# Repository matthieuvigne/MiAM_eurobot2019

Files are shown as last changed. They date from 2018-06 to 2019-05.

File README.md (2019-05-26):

# MiAM_eurobot2019
## Electronics and code of MiAM's robot for Eurobot 2019.

This repo contains code and electronics design files related the 2019 Eurobot competition of MiAM,
a French team of former students from MINES ParisTech and Arts et Métiers schools.

For older files related to the 2018 robot setup, see [MiAM_eurobot2018](https://github.com/matthieuvigne/MiAM_eurobot2018) repo.
The 2019 repo started from the 2018, but has adapted to the new robot architecture (motors, sensors...)

See [MiAM website](https://www.miam-robotique.fr/) (in French).

### Contents
 - [**ArduinoFunnyAction**](./ArduinoFunnyAction) and [**ArduinoSlave**](./ArduinoSlave): arduino code for the funny action (experiment) and for the Raspberry pi slave
 of the main robot.
 - [**ConfigRPi**](./ConfigRPi): Inscruction for configuring a raspberry pi to have headless wifi connection and to run our code.
 - [**Electronics**](./Electronics): wiring diagram and PCBs for the main robot.
 - [**RobotCode**](./RobotCode): onboard C++ code, running on Beaglebone Black or Raspberry pi processor.
 - [**miam_py**](./miam_py): a python package for reading and plotting a log file from the robot.
 - [**StrategyViewer**](./StrategyViewer): A GTK+-based viewer for the trajectories for the robots.

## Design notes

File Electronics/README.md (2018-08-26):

# Electronics

This folder contains the general wiring diagram of the robot, along with schematics and PCB files for custom boards,
realised with Kicad.

 - RPiShield: a somewhat generic shield ("hat") for the Raspberry Pi, to make GPIO and serial connections easier. This
 shield exposes, in a well-ordered manner:
	- the I2C port, with several pins to easily wire multiple salves.
	- three SPI ports (SPI0.0, SPI0.1 and SPI1.2), with a buffer protecting the CS line (useful for the L6470 breakout board,
	where this line is driven high at startup, possibly before the Raspberry Pi is powered up).
	- the UART port.
	- both hardware PWM pins.
	- three onboard LEDs.
	- the remaining 8 GPIOs.
 Note that this shield does not include any buffering on GPIOs.

 - library: a folder containing a Kicad library "MiAM", containing random custom parts used in these boards.

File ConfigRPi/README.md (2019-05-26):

# Configuration steps for Raspberry Pi setup.

This guide describes the setup guide for getting a Raspberry Pi 3 working for our robot. Beside OS install, this includes
network configuration and enabling serial ports. Example files are included in this folder for quicker setup.

## OS and ethernet config.

 - Download the latest image of [Raspbian](https://www.raspberrypi.org/downloads/raspbian/)
 (here without desktop, but you can take the desktop image if needed). Current version: 4.14 kernel, release date 2018-06-27.
 - Extract img file to SD card (this creates a partition called rootfs).
 - Enable ssh on startup by creating an empty ssh file in boot partition (not /boot folder).
 - Edit /etc/dhcpcd.conf to have a static fallback address. I will use 192.168.8.2 as the Beaglebone Black uses 192.168.7.2.
 This is done by adding the following lines to the file:
```
define static profile
    profile static_eth0
    static ip_address=192.168.8.2/24

interface eth0
    fallback static_eth0
```

 - Boot the RPi and connect to PC with ethernet.
 - Give a static IP address to your PC: sudo ip addr add 192.168.8.3/24 dev <pc_ethernet_adapter_name>
 - Connect to ssh to RPI (username pi, password raspberry) at 192.168.8.2.
 - Use raspi-config to enable UART, I2C and SPI ports. The corresponding files should appear in /dev/

## Additional package install
 - Connect RPi to the internet, through wifi: use raspi-config for that.
  sudo apt-get update
  sudo apt-get upgrade
 - Update RPi, and install hostapd, dnsmasq (wifi config) rng-tools (for random number / wifi authentification) and i2c utils.
  sudo apt-get install hostapd dnsmasq i2c-tools rng-tools
 - Install glib library.
sudo apt-get install libglib2.0-dev

## Wifi config

We will now configure the wifi adapter to broadcast a network to connect to the raspberry pi.
See: https://www.raspberrypi.org/documentation/configuration/wireless/access-point.md

 - Reset wpa_supplicant config file, if needed (to prevent autoconnect to another wifi network).
 - Use hostapd to create the network: create a file /etc/hostapd/hostapd.conf with the following content:

interface=wlan0
driver=nl80211
bridge=br0
ssid=<NetworkName>
channel=1
wmm_enabled=0
wpa=1
wpa_passphrase=<Password>
wpa_key_mgmt=WPA-PSK
wpa_pairwise=TKIP
rsn_pairwise=CCMP
auth_algs=1

 - Give a static IP address to the raspberry pi: append to /etc/dhcpcd.conf
	interface wlan0
		static ip_address=192.168.6.2/24
		nohook wpa_supplicant

 - Use dnsmasq to run a dhcp server, giving adress to a PC trying to connect to the raspberry.
 Create a file /etc/dnsmasq.conf with the following content:

  interface=wlan0
	dhcp-range=192.168.6.3,192.168.6.20,255.255.255.0,24h

 - Run on startup: edit /etc/default/hostapd to add
	DAEMON_CONF="/etc/hostapd/hostapd.conf"

	sudo systemctl start hostapd
	sudo systemctl start dnsmasq

 - To connect back to another wifi, simply comment the config in /etc/dhcpcd.conf.

## Image creation and usage.

An image with this config was created (with default password, network RaspberryPi/password RaspberryPi) using the following command:
sudo dd bs=4M if=/dev/mmcblk0 | gzip > 20180813-Raspbian4-14.img.gz
To restore, use:
cat 20180813-Raspbian4-14.img.gz | gunzip | dd of=/dev/mmcblk0

20190504-Raspbian4-19.img.gz : newer image, kernel updated to 4.19, GLIBC to 2.28.

## Running match code at startup

For Eurobot, we want our code to start automatically once the boot process is complete. To do that, we use systemd to
launch a script that starts our code. More precisely, it will launch the file /home/pi/MatchCode on startup. If this file
is not present, the boot process continues normally. Note that, once the code has started, it will conflit with
a user-launched code from ssh: to kill it, use ```pkill MatchCode```

 - Create a bash script StartMatchCode.sh to run our code, with the following content:
 ```
 #!/bin/bash
sleep 1
/home/pi/MatchCode
 ```

 - Make this file executable and store it in /etc/init.d directory:

```
 chmod +x StartMatchCode.sh
 sudo cp StartMatchCode.sh /etc/init.d/
```

 - Create the service configuration file, named StartMatchCode.service:

 ```
[Unit]
Description=Start match code
After=multi-user.target
[Service]
Type=simple
ExecStart=/etc/init.d/StartMatchCode.sh
User=pi
[Install]
WantedBy=multi-user.target
```

 - Copy the file to systemd lookup directory, then enable the service:

 ```
sudo cp StartMatchCode.service /lib/systemd/system/
sudo systemctl daemon-reload
sudo systemctl enable StartMatchCode.service
```

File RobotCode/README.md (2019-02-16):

# Robot Code
This folder contains all the code of the on-board main processor of the robot: Beaglebone Black (2018 robot) or Raspberry Pi.
This code, written entirely in C, is organished around a library, named MiAMEurobot, that implements all low-level
functionalities needed to use the robot (mainly port activation, motor and sensor drivers...). This library is
generic, and could be reused for other projects.

This folder also contains:
 - TestSensors: a simple sensor test. This code tests all the sensors of the robot, both for code debugging and wiring testing purposes.
 - EurobotCode: the main code of the robot, used for Eurobot itself.
 - DrivetrainTest: code for a simplified drivetrain used to test new components: motors, encoders...
 - HardwareTests: a set of independant tests for the robot hardware (mainly used for wiring tests).

## Compiling this code

This code is packaged in such a way as to be cross-compiled from a PC. Cross-compiling indeed has several advantages, the main
one being that there is no need to copy the source to the Beaglebone, thus preventing any temptation to developed on the board itself
(which can be a bad idea if for instance the Beaglebone dies - due to a USB cable short-circuit, I once lost code that way), and making
it very easy to replace the Beaglebone by any other. Other advantages include faster compilation, and the possibility to test compilation
without any access to the Beaglebone.

This code relies on the [glib](https://developer.gnome.org/glib/) - this choice was made to have a single, unified external library for the whole code.
Thus, to cross-compile this code, one needs:

 - a C cross compiler targeting arm platforms.
 - the glib-2.0 library, cross-compiled.

To obtain this, you may do you own setup, or follow the provided guide in ARMCrossCompilationSetup.pdf.

*Note: this identical setup can be used for cross-compiling C code to a Raspberry Pi, as it is also an arm processor.*

## Compiling and installing the BBBEurobot library.

This library, like the rest of this code, is packaged using cmake. To install it to the folder `<installPath>`, simply run:

```
	cmake /path/to/BBBEurobot -DCMAKE_INSTALL_PREFIX=<installPath>
	make
	make install
```

Once installed, this library can be imported using pkg-config. During install, the pkg-config file `BBBEurobot.pc` is installed in
`<installPath>/lib/pkgconfig` : this path must thus be added to the `PKG_CONFIG_PATH` variable. To do so, open your `.bashrc` file

```
gedit ~/.bashrc
```

and append the following line :

```
export PKG_CONFIG_PATH=<installPath>/lib/pkgconfig
```

Remember to `source ~/.bashrc` before use.

There is a doxygen documentation for this library in `BBBEurobot/doc`. Simply run `make_documentation.sh` to generate it.

## Running code of the Beaglebone.

Obviously, the code we have written aims at using the BeagleBone GPIOs and serial ports. To access these ports, the Beaglebone needs a
device tree overlay (DTO) file to enable these ports.
A DTO file for BBB-Eurobot, enabeling all the ports exposed on the PCB (plus UART4, which is needed to talk to the servo driver - it wasn't planned
on the PCB but a wire can easily be solder to make this connection. Note that you need a 3.3V to 5V converter).

This file is called Eurobot-00A0.dts, and can be found in the library folder (BBB-Eurobot). To use it, copy this file to the Beaglebone,
then compile it and copy it to /lib/firmware:

```
	dtc -O dtb -o Eurobot-00A0.dtbo -b 00 -@ Eurobot-00A0.dts
	cp Eurobot-00A0.dtbo /lib/firmware
```

Now doing ```echo Eurobot > /sys/devices/bone_capemgr.9/slots``` enables all these ports for the duration of the current boot (this is done internally by BBB-Eurobot).

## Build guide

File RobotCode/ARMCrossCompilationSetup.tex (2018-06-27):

\documentclass[a4paper,11pt]{article}
\usepackage[T1]{fontenc}
\usepackage[utf8]{inputenc}
\usepackage{lmodern}
\usepackage[english]{babel}
\usepackage{hyperref}
\usepackage{listings}

%listings settings
\lstset{
  basicstyle=\ttfamily,
  columns=fullflexible,
  frame=leftline,
  rulecolor=\color{red},
  framerule=2pt,
  xleftmargin=15pt,
  breaklines=true
}

\hypersetup{
  colorlinks   = true, %Colours links instead of ugly boxes
  urlcolor     = blue, %Colour for external hyperlinks
  linkcolor    = black, %Colour of internal links
  citecolor   = black %Colour of citations
}

\title{Cross-compilation environment setup.}
\author{Matthieu Vigne}

\begin{document}
\maketitle
\tableofcontents
\section{Introduction}

\par This guide explains how to setup a cross-compilation environment on a Linux PC (Fedora or Debian/Ubunu) to compile our code, i.e. the BBBEurobot library. This setup works for compiling code to a Beaglebone Black, and to a Raspberry Pi as well.
Three things are needed to cross-compile this code:

 - a C compiler targeting the \emph{armhf} platform, called \textbf{gcc-arm-linux-gnueabihf}.
 
 - a cross-compiled version of the glib, used by our code.
 
 - a renamed \emph{pkg-config} file to load the cross-compiled glib when compiling.
 
\section{Debian setup}

These instructions were tested on Debian 8 (Jessie) in 2015. The setup for Ubuntu is probably quite similar.

Setup on Debian is quite fast, as the official repo already have the compiler and a cross-compiled glib. The only step needed is to tell \emph{apt} to add the arm platform, then install the packages as usual:

\begin{lstlisting}[]
sudo dpkg --add-architecture armhf
sudo apt-get update
sudo apt-get install gcc-arm-linux-gnueabihf
sudo apt-get install libglib2.0-dev:armhf
\end{lstlisting}

Now everything is installed, but there is one last setup step needed: link to the \emph{pkg-config} file of the glib. Since it has the same name as the one installed for your system library version, we will rename it to prevent any conflict. To keep things clear, I advise you modify (freely) the \emph{Name:} and \emph{Description:} fields of this file, \emph{/usr/lib/arm-linux-gnueabihf/pkgconfig/glib-2.0.pc} though for instance the following command:

\begin{lstlisting}
sudo nano /usr/lib/arm-linux-gnueabihf/pkgconfig/glib-2.0.pc
\end{lstlisting}

Then, simply copy this file to the default \emph{pkg-config} search path, renaming it:

\begin{lstlisting}[]
sudo mv /usr/lib/arm-linux-gnueabihf/pkgconfig/glib-2.0.pc /usr/share/pkgconfig/armglib-2.0.pc
\end{lstlisting}

To check that everything works correctly, type:

\begin{lstlisting}[]
pkg-config --list-all | grep arm
\end{lstlisting}

This should give you the \emph{armglib-2.0} library, with the name and description you previously entered.

\section{Fedora setup}

These instructions were tested in Febuary 2018 on Fedora 27.

Contrary to Debian, the official Fedora repo do not contain either the compiler nor the cross-compiled glib. We will get the compiler from an unofficial Copr repo, and then cross-compile the glib from source.

First, install the compiler and cross-compiled glibc (for basic C functions: this is a dependency of glib) using:

\begin{lstlisting}
sudo dnf copr enable lantw44/arm-linux-gnueabihf-toolchain
sudo dnf install arm-linux-gnueabihf-gcc arm-linux-gnueabihf-glibc
\end{lstlisting}

In order to compile the glib, we must first install its dependencies.

The firs is libffi: get the latest version from  \href{https://sourceware.org/libffi/}{https://sourceware.org/libffi/} (v 3.2.1 in Febuary 2018), decompress it, then run from the source folder:

\begin{lstlisting}[]
./configure --host=arm-linux-gnueabihf --prefix=/usr/arm-linux-gnueabihf/sys-root/
make
sudo make install
\end{lstlisting}

The first line configures the build, telling the system to cross-compile the library using the cross-compiler instead of system gcc, and to install it in \emph{/usr/arm-linux-gnueabihf/sys-root/}, the path used on install of the compiler and glibc. Then we compile and install the library.

\emph{Note: for faster compilation, you can append \emph{-jN} to the make instruction, where N is the number of process being run in parallel.}

The second dependancy is the zlib (\href{http://www.zlib.net/}{http://www.zlib.net/}, v 1.2.11 in Febuary 2018), installed with the same process:
\begin{lstlisting}[]
CC=arm-linux-gnueabihf-gcc ./configure --prefix=/usr/arm-linux-gnueabihf/sys-root/
make
sudo make install
\end{lstlisting}

Finally, download the glib \href{http://ftp.gnome.org/pub/GNOME/sources/glib/}{http://ftp.gnome.org/\\pub/GNOME/sources/glib/} (v 2.55.1 in Febuary 2018). Go to the parent of the source directory (i.e. where you uncompressed the archive), create a build folder, in which we place a config file \emph{arm.cache}:

\begin{lstlisting}
mkdir build
cd build
gedit arm.cache
\end{lstlisting}

Copy the following content in \emph{arm.cache}:
\begin{lstlisting}[caption= File arm.cache]
glib_cv_long_long_format=ll
glib_cv_stack_grows=no
glib_cv_uscore=yes
ac_cv_func_posix_getpwuid_r=no
ac_cv_func_posix_getgrgid_r=no
LIBFFI_CFLAGS="-I/usr/arm-linux-gnueabihf/sys-root/lib/libffi-3.2.1/include"
LIBFFI_LIBS="-L/usr/arm-gnueabihf/sys-root/lib -lffi"
ZLIB_CFLAGS="-I/usr/arm-linux-gnueabihf/sys-root/include"
ZLIB_LIBS="-L/usr/arm-linux-gnueabihf/sys-root/lib -lz"
\end{lstlisting}

Now, configure the build using the given \emph{arm.cache}:

\begin{lstlisting}[]
../glib-2.55.1/configure --host=arm-linux-gnueabihf --prefix=/usr/arm-linux-gnueabihf/sys-root/ --cache-file=./arm.cache --with-pcre --enable-libmount=no
make
sudo make install
\end{lstlisting}

Comments: the option --with-pcre tells the configuration script to use internally-package pcre library. --enable-libmount=no disables libmount, a library used for disk mounting that we won't be using on the Beaglebone, and hence that wasn't installed (it can otherwise be installed using the same process as before).

Now everything is installed, but there is one last setup step needed: link to the \emph{pkg-config} file of the glib. Since it has the same name as the one installed for your system library version, we will rename it to prevent any conflict. To keep things clear, I advise you modify (freely) the \emph{Name:} and \emph{Description:} fields of this file, \emph{/usr/arm-linux-gnueabihf/sys-root/lib/pkgconfig/glib-2.0.pc} though for instance the following command:

\begin{lstlisting}
sudo nano /usr/arm-linux-gnueabihf/sys-root/lib/pkgconfig/glib-2.0.pc
\end{lstlisting}

Then, simply copy this file to the default \emph{pkg-config} search path, renaming it:

\begin{lstlisting}[]
sudo mv /usr/arm-linux-gnueabihf/sys-root/lib/pkgconfig/glib-2.0.pc /usr/share/pkgconfig/armglib-2.0.pc
\end{lstlisting}

To check that everything works correctly, type:

\begin{lstlisting}[]
pkg-config --list-all | grep arm
\end{lstlisting}

This should give you the \emph{armglib-2.0} library, with the name and description you previously entered.

\end{document}

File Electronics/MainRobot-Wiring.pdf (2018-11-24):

# MiAM main robot electrical architecture

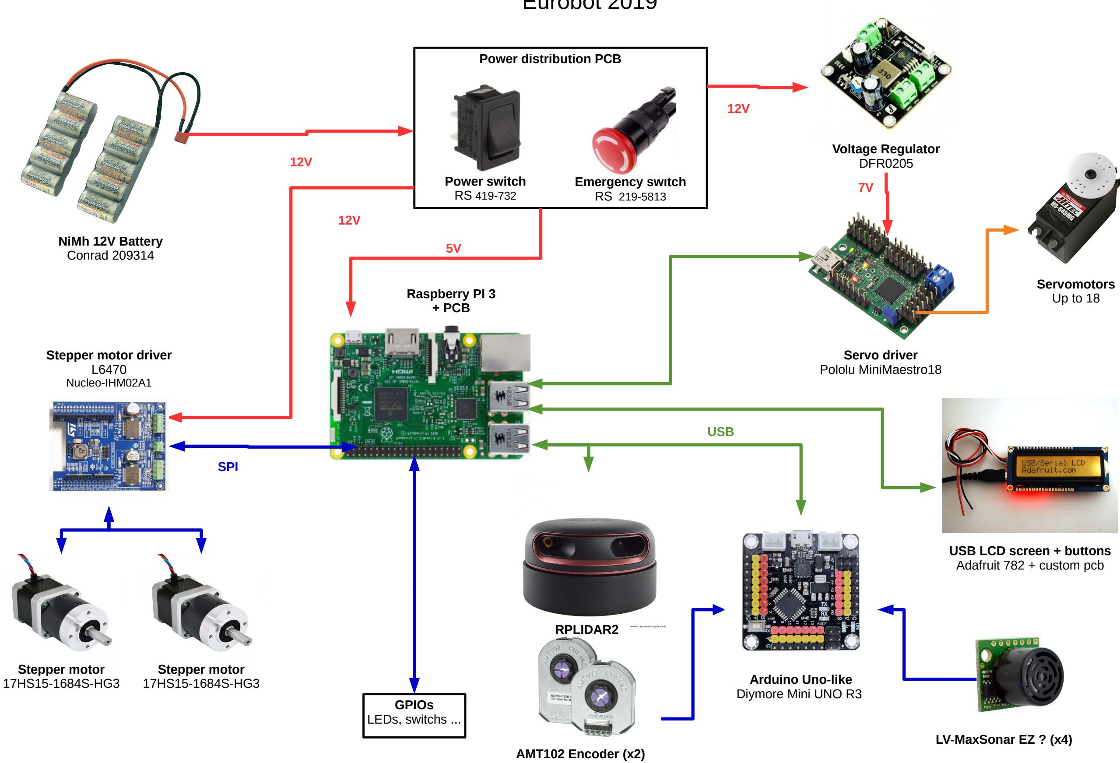
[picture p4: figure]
SPI; NiMh 12V Battery Conrad 209314; Servo driver Pololu MiniMaestro18; Power switch RS 419-732; Emergency switch RS 219-5813; Power distribution PCB; USB; AMT102 Encoder (x2); Arduino Uno-like Diymore Mini UNO R3; LV-MaxSonar EZ ? (x4); Servomotors Up to 18; Voltage Regulator DFR0205; GPIOs LEDs, switchs ...; Raspberry PI 3 + PCB; USB LCD screen + buttons Adafruit 782 + custom pcb; Stepper motor driver L6470 Nucleo-IHM02A1; Stepper motor 17HS15-1684S-HG3; RPLIDAR2

# Eurobot 2019

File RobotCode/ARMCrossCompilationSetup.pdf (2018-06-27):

Cross-compilation environment setup.

Matthieu Vigne

May 27, 2018

## Contents

1 Introduction | 1
2 Debian setup | 1
3 Fedora setup | 2

## 1 Introduction

This guide explains how to setup a cross-compilation environment on a Linux PC (Fedora or Debian/Ubunu) to compile our code, i.e. the BBBEurobot library. This setup works for compiling code to a Beaglebone Black, and to a Raspberry Pi as well. Three things are needed to cross-compile this code:
- a C compiler targeting the armhf platform, called gcc-arm-linux-gnueabihf.
- a cross-compiled version of the glib, used by our code.
- a renamed pkg-config file to load the cross-compiled glib when compiling.

## 2 Debian setup

These instructions were tested on Debian 8 (Jessie) in 2015. The setup for Ubuntu is probably quite similar.
Setup on Debian is quite fast, as the official repo already have the compiler and a cross-compiled glib. The only step needed is to tell apt to add the arm platform, then install the packages as usual:

sudo dpkg --add-architecture armhf
sudo apt-get update
sudo apt-get install gcc-arm-linux-gnueabihf sudo apt-get install libglib2.0-dev:armhf

1

Now everything is installed, but there is one last setup step needed: link to the pkg-config file of the glib. Since it has the same name as the one installed for your system library version, we will rename it to prevent any conflict. To keep things clear, I advise you modify (freely) the Name: and Description: fields of this file, /usr/lib/arm-linux-gnueabihf/pkgconfig/glib-2.0.pc though for instance the following command:

sudo nano /usr/lib/arm-linux-gnueabihf/pkgconfig/glib-2.0.pc

Then, simply copy this file to the default pkg-config search path, renaming it:

sudo mv /usr/lib/arm-linux-gnueabihf/pkgconfig/glib-2.0.pc / usr/share/pkgconfig/armglib-2.0.pc

To check that everything works correctly, type:

pkg-config --list-all | grep arm

This should give you the armglib-2.0 library, with the name and description you previously entered.

## 3 Fedora setup

These instructions were tested in Febuary 2018 on Fedora 27.
Contrary to Debian, the official Fedora repo do not contain either the compiler nor the cross-compiled glib. We will get the compiler from an unofficial Copr repo, and then cross-compile the glib from source.
First, install the compiler and cross-compiled glibc (for basic C functions: this is a dependency of glib) using:

sudo dnf copr enable lantw44/arm-linux-gnueabihf-toolchain sudo dnf install arm-linux-gnueabihf-gcc arm-linux-gnueabihf -glibc

In order to compile the glib, we must first install its dependencies.
The firs is libffi: get the latest version from https://sourceware.org/libffi/(v 3.2.1 in Febuary 2018), decompress it, then run from the source folder:

./configure --host=arm-linux-gnueabihf --prefix=/usr/armlinux-gnueabihf/sys-root/
make
sudo make install

The first line configures the build, telling the system to cross-compile the library using the cross-compiler instead of system gcc, and to install it in /usr/arm-linux-gnueabihf/sys-root/, the path used on install of the compiler and glibc. Then we compile and install the library.
Note: for faster compilation, you can append -jN to the make instruction, where N is the number of process being run in parallel.

2

The second dependancy is the zlib (http://www.zlib.net/, v 1.2.11 in Febuary 2018), installed with the same process:

CC=arm-linux-gnueabihf-gcc ./configure --prefix=/usr/armlinux-gnueabihf/sys-root/
make
sudo make install

Finally, download the glib http://ftp.gnome.org/pub/GNOME/sources/glib/ (http://ftp.gnome.org/pub/GNOME/sources/glib/) (v 2.55.1 in Febuary 2018). Go to the parent of the source directory (i.e. where you uncompressed the archive), create a build folder, in which we place a config file arm.cache:

mkdir build
cd build
gedit arm.cache

Copy the following content in arm.cache:

Listing 1: File arm.cache

glib_cv_long_long_format=ll glib_cv_stack_grows=no
glib_cv_uscore=yes
ac_cv_func_posix_getpwuid_r=no ac_cv_func_posix_getgrgid_r=no LIBFFI_CFLAGS="-I/usr/arm-linux-gnueabihf/sys-root/lib/ libffi-3.2.1/include"
LIBFFI_LIBS="-L/usr/arm-gnueabihf/sys-root/lib -lffi" ZLIB_CFLAGS="-I/usr/arm-linux-gnueabihf/sys-root/include" ZLIB_LIBS="-L/usr/arm-linux-gnueabihf/sys-root/lib -lz"

Now, configure the build using the given arm.cache:

../glib-2.55.1/configure --host=arm-linux-gnueabihf --prefix =/usr/arm-linux-gnueabihf/sys-root/ --cache-file=./arm. cache --with-pcre --enable-libmount=no
make
sudo make install

Comments: the option –with-pcre tells the configuration script to use internally-package pcre library. –enable-libmount=no disables libmount, a library used for disk mounting that we won’t be using on the Beaglebone, and hence that wasn’t installed (it can otherwise be installed using the same process as before).
Now everything is installed, but there is one last setup step needed: link to the pkg-config file of the glib. Since it has the same name as the one installed for your system library version, we will rename it to prevent any conflict. To keep things clear, I advise you modify (freely) the

3

Name: and Description: fields of this file, /usr/arm-linux-gnueabihf/sys-root/lib/pkgconfig/glib-2.0.pc though for instance the following command:

sudo nano /usr/arm-linux-gnueabihf/sys-root/lib/pkgconfig/ glib-2.0.pc

Then, simply copy this file to the default pkg-config search path, renaming it:

sudo mv /usr/arm-linux-gnueabihf/sys-root/lib/pkgconfig/glib -2.0.pc /usr/share/pkgconfig/armglib-2.0.pc

To check that everything works correctly, type:

pkg-config --list-all | grep arm

This should give you the armglib-2.0 library, with the name and description you previously entered.

4

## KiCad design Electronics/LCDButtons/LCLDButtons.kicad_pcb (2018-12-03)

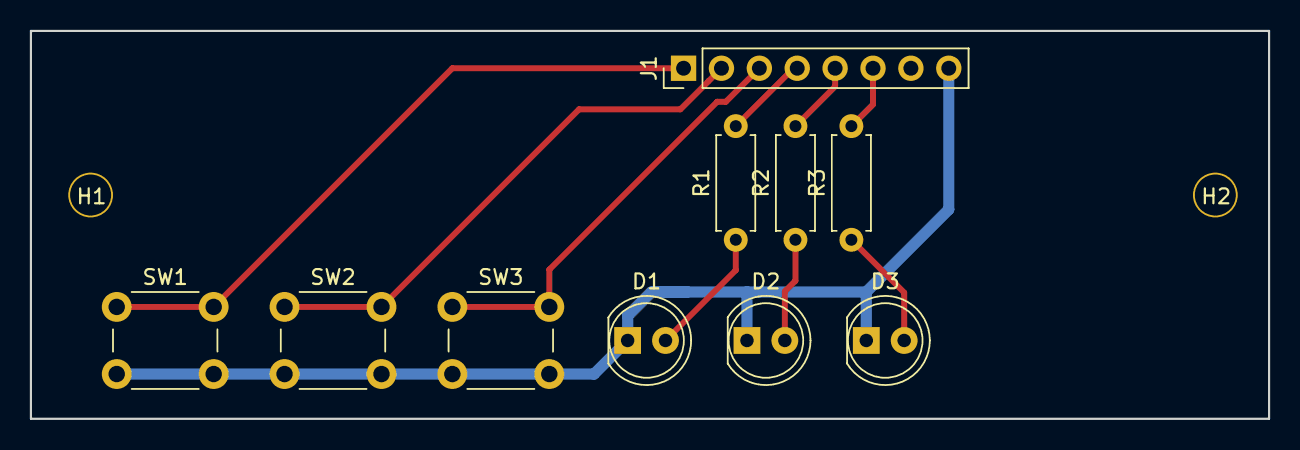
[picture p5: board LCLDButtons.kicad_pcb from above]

Board: 2 copper layers, 83.0 x 26.0 mm, 12 parts (0 on the bottom side), 10 nets.

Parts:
D1, D2, D3: LED; LED_D5.0mm
H1, H2: Hole_3mm_PTH; NPTH_3mm_ID
J1: Conn_01x08; Pin_Header_Straight_1x08_Pitch2.54mm
R1, R2, R3: 1k; R_Axial_DIN0207_L6.3mm_D2.5mm_P7.62mm_Horizontal
SW1, SW2, SW3: SW_SPST; SW_PUSH_6mm

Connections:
/PB0: J1.4, R1.2
/PC2: J1.3, SW3.1
/PC4: J1.2, SW2.1
/PC7: J1.1, SW1.1
/RX: J1.6, R3.2
/TX: J1.5, R2.2
GND: D1.1, D2.1, D3.1, J1.8, SW1.2, SW2.2, SW3.2
unnamed: D1.2, R1.1
unnamed: D2.2, R2.1
unnamed: D3.2, R3.1

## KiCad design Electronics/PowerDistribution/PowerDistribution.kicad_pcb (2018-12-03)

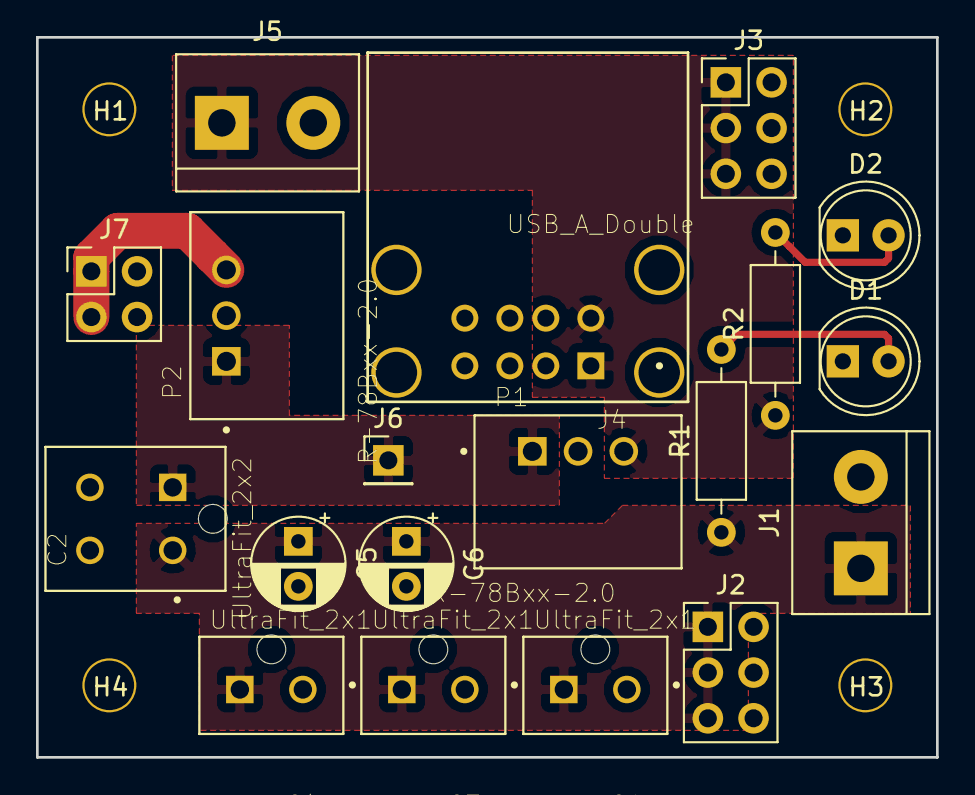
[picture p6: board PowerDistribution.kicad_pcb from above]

Board: 2 copper layers, 50.0 x 40.0 mm, 23 parts (0 on the bottom side), 7 nets.

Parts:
C1, C3, C4: UltraFit_2x1; MOLEX_1722861102
C2: UltraFit_2x2; MOLEX_1722981104
C5, C6: CP1; CP_Radial_D5.0mm_P2.50mm
D1, D2: LED; LED_D5.0mm
H1, H2, H3, H4: Hole_3mm_PTH; NPTH_3mm_ID
J1, J5: Screw_Terminal_01x02; TerminalBlock_bornier-2_P5.08mm
J2, J3: Conn_02x03_Odd_Even; PinHeader_2x03_P2.54mm_Vertical
J4: USB_A_Double; USB_A_Double_2410_05
J6: Conn_01x01_Male; PinHeader_1x01_P2.54mm_Vertical
J7: Conn_02x02_Odd_Even; PinHeader_2x02_P2.54mm_Vertical
P1, P2: R-78Bxx-2.0; CONV_R-78Bxx-2.0
R1: 2k; R_Axial_DIN0207_L6.3mm_D2.5mm_P10.16mm_Horizontal
R2: 600; R_Axial_DIN0207_L6.3mm_D2.5mm_P10.16mm_Horizontal

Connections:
+12V: C2.1, J6.1, P1.1, P2.1
GND: C1.2, C2.4, C3.2, C4.2, C5.2, C6.2, D1.1, D2.1, J1.2, J2.2, J2.4, J2.6, J3.2, J3.4, J3.6, J4.4, J5.2, J7.2, J7.4, P1.2, P2.2
unnamed: C1.1, C2.2, C3.1, C4.1, C5.1, C6.1, J1.1, J2.1, J2.3, J2.5, R1.1
unnamed: D1.2, R1.2
unnamed: D2.2, R2.2
unnamed: J3.1, J3.3, J3.5, J4.1, J5.1, P1.3, R2.1
unnamed: J7.1, J7.3, P2.3

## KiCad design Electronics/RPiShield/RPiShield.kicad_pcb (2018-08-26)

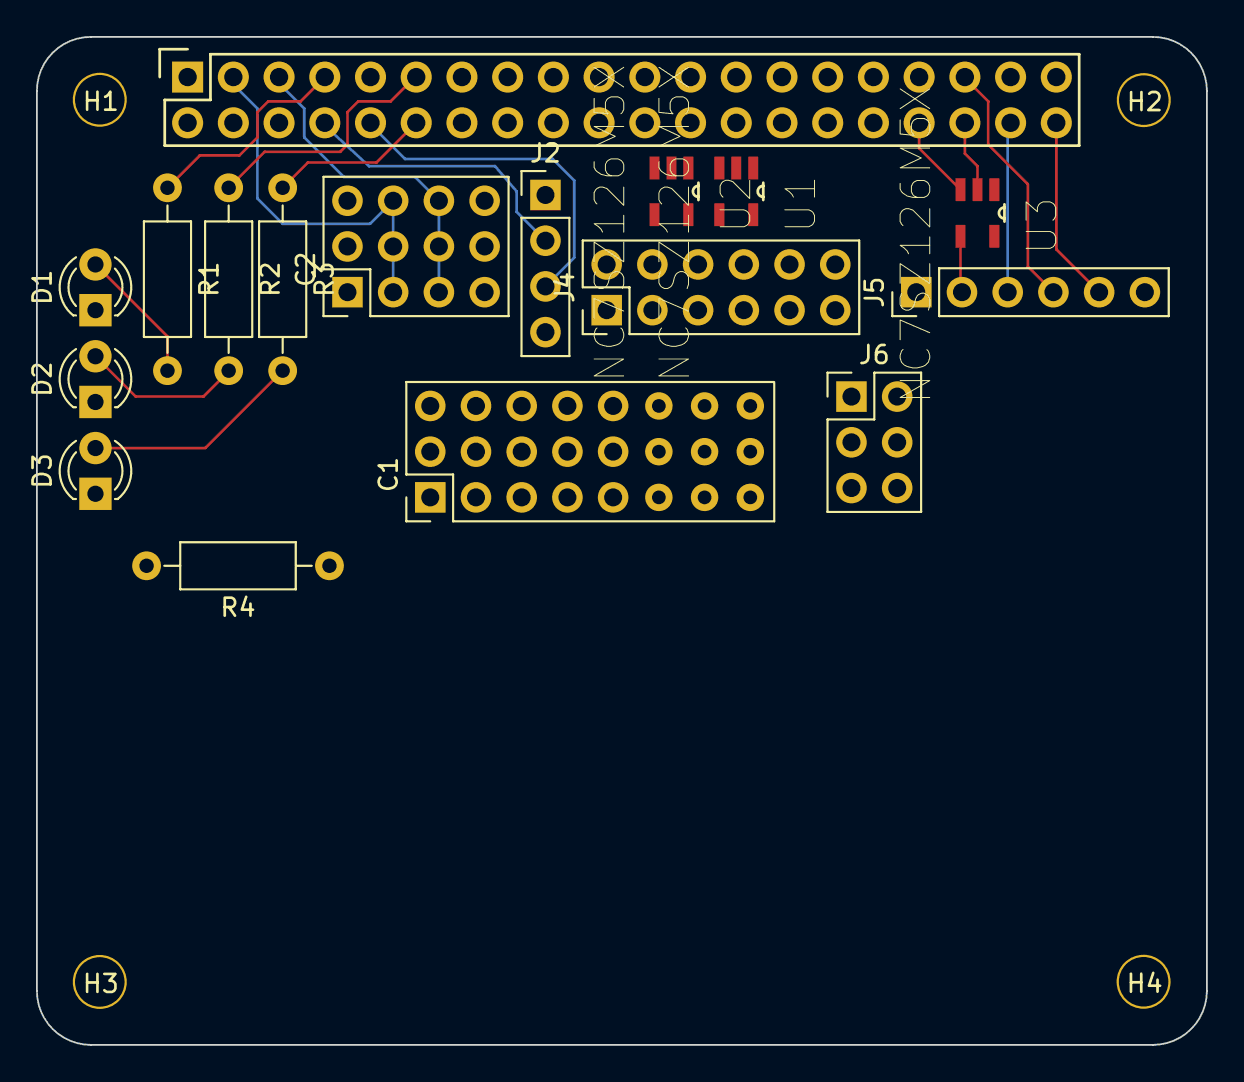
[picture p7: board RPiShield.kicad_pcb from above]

Board: 2 copper layers, 65.0 x 56.0 mm, 21 parts (0 on the bottom side), 35 nets.

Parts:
C1: Conn_03x08; Pin_Header_Straight_3x08_Pitch2.54mm
C2: Conn_03x04; Pin_Header_Straight_3x04_Pitch2.54mm
D1, D2, D3: LED; LED_D3.0mm
H1, H2, H3, H4: Hole_3mm_PTH; NPTH_3mm_ID
J1: PI40HAT; Socket_Strip_Straight_2x20
J2: Conn_01x04; Pin_Header_Straight_1x04_Pitch2.54mm
J4: Conn_02x06_Odd_Even; Pin_Header_Straight_2x06_Pitch2.54mm
J5: Conn_01x06; Pin_Header_Straight_1x06_Pitch2.54mm
J6: Conn_02x03_Odd_Even; Pin_Header_Straight_2x03_Pitch2.54mm
R1, R2, R3: 220; R_Axial_DIN0207_L6.3mm_D2.5mm_P10.16mm_Horizontal
R4: 20k; R_Axial_DIN0207_L6.3mm_D2.5mm_P10.16mm_Horizontal
U1, U2, U3: NC7SZ126M5X

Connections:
+3V3: C1.2, C1.5, C1.8, C1.11, C1.14, C1.17, C1.20, C1.23, C2.1, C2.2, C2.3, J1.1, J1.17, J2.1, J4.1, J4.2, J5.1, J6.3, J6.4, R4.1, U1.1, U1.5, U2.1, U2.5, U3.1, U3.5
+5V: J1.2, J1.4
/GPIO_5: C1.18, J1.29
/GPIO_6: C1.21, J1.31
/GPIO_12_PWM0: J1.32, J6.1
/GPIO_13_PWM1: J1.33, J6.2
/GPIO_22: C1.6, J1.15
/GPIO_23: C1.9, J1.16
/GPIO_24: C1.12, J1.18
/GPIO_25: C1.15, J1.22
/GPIO_26: C1.24, J1.37
/GPIO_27: C1.3, J1.13
/I2C_SCL: C2.7, C2.8, C2.9, J1.5
/I2C_SDA: C2.4, C2.5, C2.6, J1.3
/SPI0_CLK: J1.23, J4.9, J4.10
/SPI0_MISO: J1.21, J4.7, J4.8
/SPI0_MOSI: J1.19, J4.5, J4.6
/SPI0_SS0: J1.24, U1.2
/SPI0_SS1: J1.26, U2.2
/SPI1_CLK: J1.40, J5.5
/SPI1_MISO: J1.35, J5.4
/SPI1_MOSI: J1.38, J5.3
/SPI1_SS2: J1.36, U3.2
/UART_RX: J1.10, J2.3
/UART_TX: J1.8, J2.2
GND: C1.1, C1.4, C1.7, C1.10, C1.13, C1.16, C1.19, C1.22, C2.10, C2.11, C2.12, D1.1, D2.1, D3.1, J1.6, J1.9, J1.14, J1.20, J1.25, J1.30, J1.34, J1.39, J2.4, J4.11, J4.12, J5.6, J6.5, J6.6, R4.2, U1.3, U2.3, U3.3
unnamed: D1.2, R1.2
unnamed: D2.2, R2.2
unnamed: D3.2, R3.2
unnamed: J1.7, R1.1
unnamed: J1.11, R2.1
unnamed: J1.12, R3.1
unnamed: J4.3, U1.4
unnamed: J4.4, U2.4
unnamed: J5.2, U3.4

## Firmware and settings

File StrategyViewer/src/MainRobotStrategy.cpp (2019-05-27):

/// \author Matthieu Vigne
/// \copyright GNU GPLv3
#include "ViewerRobot.h"
#include <MiAMEurobot/trajectory/Utilities.h>
#include <MiAMEurobot/trajectory/ArcCircle.h>

using namespace miam::trajectory;

// Define robot constants for trajectory generation.
namespace robotdimensions
{
    double const wheelSpacing = 106.0; ///< Wheel spacing from robot center, in mm.
    double const maxWheelSpeedTrajectory = 400; ///< Maximum wheel speed, in mm/s.
    double const maxWheelAccelerationTrajectory = 400; ///< Maximum wheel acceleration, in mm/s^2.
}

// Robot dimension.
double const CHASSIS_FRONT = 150.0;
double const CHASSIS_BACK = 150.0;
double const CHASSIS_WIDTH = 150.0;


void mainRobotStrategy(ViewerRobot &robot)
{
    robot.trajectory_.clear();
    robot.clearScore();
    std::cout << "Computing main robot strategy, obstacle at " << robot.obstacleX_ << " " << robot.obstacleY_ << std::endl;

    // Update config.
    miam::trajectory::setTrajectoryGenerationConfig(robotdimensions::maxWheelSpeedTrajectory,
                                                    robotdimensions::maxWheelAccelerationTrajectory,
                                                    robotdimensions::wheelSpacing);

    // Create required variables.
    RobotPosition targetPosition;
    TrajectoryVector traj;
    RobotPosition endPosition;
    std::vector<RobotPosition> positions;
    bool wasMoveSuccessful = true;

    // Set initial position
    targetPosition.x = CHASSIS_WIDTH + 75;
    targetPosition.y = 1100 + CHASSIS_FRONT + 30;
    targetPosition.theta = -M_PI_2;
    robot.resetPosition(targetPosition, true, true, true);

    //**********************************************************
    // Go get first atoms.
    //**********************************************************
    targetPosition.y = CHASSIS_FRONT + 50;
    traj = miam::trajectory::computeTrajectoryStraightLineToPoint(robot.getCurrentPosition(), targetPosition);
    robot.setTrajectoryToFollow(traj);
    wasMoveSuccessful = robot.waitForTrajectoryFinished();

    //~ getAtoms();
    //~ robot.moveRail(0.05);
    //~ robot.servos_.moveSuction(false);

    // Move back on base, drop all three atoms.
    targetPosition.y = 1710;
    traj = miam::trajectory::computeTrajectoryStraightLineToPoint(robot.getCurrentPosition(), targetPosition, 0.0, true);
    robot.setTrajectoryToFollow(traj);
    // Atom drop
    int suctionOrder[3] = {2, 1, 0};
    if (robot.isPlayingRightSide())
    {
        suctionOrder[0] = 0;
        suctionOrder[2] = 2;
    }
    //~ while (!robot.isTrajectoryFinished())
    //~ {
        //~ targetPosition = robot.getCurrentPosition();
        //~ if (targetPosition.y > 950)
        //~ {
            //~ robot.servos_.tapOpen();
            //~ robot.servos_.openTube(suctionOrder[0]);
        //~ }
        //~ if (targetPosition.y > 1300)
            //~ robot.servos_.openTube(suctionOrder[1]);
        //~ if (targetPosition.y > 1600)
            //~ robot.servos_.openTube(suctionOrder[2]);
        //~ usleep(20000);
    //~ }
    if (wasMoveSuccessful)
        robot.updateScore(18); // 3 atoms with the right color inside the zone.
    //~ robot.moveRail(0.3);
    //~ robot.servos_.moveSuction(true);


    //**********************************************************
    // Get second set of atoms.
    //**********************************************************

    // Go get left set of three atoms, following a curved trajectory.
    targetPosition = robot.getCurrentPosition();
    positions.push_back(targetPosition);
    targetPosition.x = 500;
    positions.push_back(targetPosition);
    targetPosition.x += 220;
    targetPosition.y -= 40;
    positions.push_back(targetPosition);
    targetPosition.y = 800;
    positions.push_back(targetPosition);
    targetPosition.x = 600;
    targetPosition.y = 700;
    positions.push_back(targetPosition);
    targetPosition.y = 510 + CHASSIS_FRONT;
    positions.push_back(targetPosition);
    traj = miam::trajectory::computeTrajectoryRoundedCorner(positions, 100.0, 0.05);
    robot.setTrajectoryToFollow(traj);
    wasMoveSuccessful = robot.waitForTrajectoryFinished();

    // Grab atoms.
    bool hasAtoms = false;
    if (wasMoveSuccessful)
    {
        //~ getAtoms();
        hasAtoms = true;
    }
    targetPosition = robot.getCurrentPosition();
    traj = miam::trajectory::computeTrajectoryStraightLine(targetPosition, -150);
    robot.setTrajectoryToFollow(traj);
    robot.waitForTrajectoryFinished();

    //~ robot.moveRail(0.05);
    //~ robot.servos_.moveSuction(false);

    // Go drop atoms.
    // Drop everything in the red zone, pushing the tree atoms on the field.
    positions.clear();
    targetPosition = robot.getCurrentPosition();
    positions.push_back(targetPosition);
    targetPosition.y = 1550;
    positions.push_back(targetPosition);
    targetPosition.x = 450;
    positions.push_back(targetPosition);
    traj = miam::trajectory::computeTrajectoryRoundedCorner(positions, 150.0, 0.05);
    robot.setTrajectoryToFollow(traj);
    wasMoveSuccessful = robot.waitForTrajectoryFinished();

    //~ robot.servos_.tapOpen();
    //~ robot.servos_.openTube(0);
    //~ robot.servos_.openTube(1);
    //~ robot.servos_.openTube(2);
    if (wasMoveSuccessful)
        robot.updateScore(13); // Three atoms pushed in the zone, two of the right color.
    if (hasAtoms)
        robot.updateScore(13); // Three atoms dropped in the zone, two of the right color.

    // Move back
    targetPosition = robot.getCurrentPosition();
    traj = miam::trajectory::computeTrajectoryStraightLine(targetPosition, -150);
    robot.setTrajectoryToFollow(traj);
    robot.waitForTrajectoryFinished();

    //**********************************************************
    // Drop the blue atom in the particle accelerator.
    //**********************************************************
    targetPosition = robot.getCurrentPosition();
    positions.clear();
    positions.push_back(targetPosition);
    targetPosition.x = 1300;
    positions.push_back(targetPosition);
    targetPosition.x = 1600;
    targetPosition.y = 2000 - CHASSIS_WIDTH - 130;
    positions.push_back(targetPosition);
    targetPosition.x = 1620;
    positions.push_back(targetPosition);
    traj = miam::trajectory::computeTrajectoryRoundedCorner(positions, 80.0, 0.1);
    robot.setTrajectoryToFollow(traj);
    //~ usleep(100000);
    //~ while (!robot.isTrajectoryFinished())
    //~ {
        //~ targetPosition = robot.getCurrentPosition();
        //~ if (targetPosition.x > 1250)
        //~ {
            //~ robot.servos_.unfoldArms(robot.isPlayingRightSide());
            //~ break;
        //~ }
    //~ }
    wasMoveSuccessful = robot.waitForTrajectoryFinished();
    //~ robot.servos_.raiseArms(robot.isPlayingRightSide());
    if (wasMoveSuccessful)
    {
        robot.updateScore(20); // 20 pts: atom + goldium release.

        //**********************************************************
        // Get the goldium atom.
        //**********************************************************
        //~ robot.moveRail(1.0);
        //~ robot.servos_.moveSuction(true);
        targetPosition = robot.getCurrentPosition();
        targetPosition.x = 3000 - 770;
        targetPosition.y = 1650;
        traj = miam::trajectory::computeTrajectoryStraightLineToPoint(robot.getCurrentPosition(), targetPosition);
        endPosition = targetPosition;
        endPosition.y = 2000 - CHASSIS_FRONT - 100;
        traj = traj + miam::trajectory::computeTrajectoryStraightLineToPoint(targetPosition, endPosition);
        robot.setTrajectoryToFollow(traj);
        wasMoveSuccessful = robot.waitForTrajectoryFinished();

        if (wasMoveSuccessful)
        {
            //~ robot.servos_.tapClose();
            //~ robot.servos_.closeTube(0);
            //~ robot.servos_.openTube(1);
            //~ robot.servos_.closeTube(2);
            //~ robot.servos_.turnOnPump();
            //~ usleep(500000);
            targetPosition = robot.getCurrentPosition();
            traj = miam::trajectory::computeTrajectoryStraightLine(targetPosition, 40);
            robot.setTrajectoryToFollow(traj);
            robot.waitForTrajectoryFinished();
            //~ usleep(500000);
            //~ robot.servos_.closeTube(2);
            //~ robot.servos_.tapClose();
            //~ usleep(500000);
            //~ robot.servos_.turnOffPump();
            //~ usleep(500000);
            traj = miam::trajectory::computeTrajectoryStraightLine(targetPosition, -150);
            robot.setTrajectoryToFollow(traj);
            robot.waitForTrajectoryFinished();
            robot.updateScore(20); // 20 pts for goldium drop.
            //~ robot.servos_.openTube(2);
        }
    }


    //**********************************************************
    // Push things from the chaos zone
    //**********************************************************
    targetPosition = robot.getCurrentPosition();
    positions.clear();
    positions.push_back(targetPosition);
    targetPosition.x = 1200;
    targetPosition.y = 950;
    positions.push_back(targetPosition);
    targetPosition.x = 500;
    positions.push_back(targetPosition);
    traj = miam::trajectory::computeTrajectoryRoundedCorner(positions, 100.0, 0.05);
    robot.setTrajectoryToFollow(traj);
    wasMoveSuccessful = robot.waitForTrajectoryFinished();
    if (wasMoveSuccessful)
        robot.updateScore(9);   // 4 atoms pushed, one of the right color.

    //**********************************************************
    // Get the last three set of atoms.
    //**********************************************************
    if (wasMoveSuccessful)
    {
        targetPosition = robot.getCurrentPosition();
        traj = miam::trajectory::computeTrajectoryStraightLine(targetPosition, -150);
        robot.setTrajectoryToFollow(traj);
        robot.waitForTrajectoryFinished();
    }
    targetPosition = robot.getCurrentPosition();
    positions.clear();
    positions.push_back(targetPosition);
    targetPosition.x = 900;
    targetPosition.y = 950;
    positions.push_back(targetPosition);
    targetPosition.y = 510 + CHASSIS_FRONT;;
    positions.push_back(targetPosition);
    traj = miam::trajectory::computeTrajectoryRoundedCorner(positions, 100.0, 0.05);
    robot.setTrajectoryToFollow(traj);
    wasMoveSuccessful = robot.waitForTrajectoryFinished();

    // Grab atoms.
    if (wasMoveSuccessful)
    {
        //~ getAtoms();
        // Go put the atoms in the right zone.
        if (robot.isPlayingRightSide())
        {
            suctionOrder[0] = 0;
            suctionOrder[1] = 0;
            suctionOrder[2] = 1;
        }
        else
        {
            suctionOrder[0] = 2;
            suctionOrder[1] = 0;
            suctionOrder[2] = 1;
        }

        // Move to blue zone.
        targetPosition = robot.getCurrentPosition();
        targetPosition.y = 950;
        traj = miam::trajectory::computeTrajectoryStraightLineToPoint(robot.getCurrentPosition(), targetPosition, 0, true);
        endPosition = targetPosition;
        endPosition.x = 450 + CHASSIS_FRONT;
        traj = traj + miam::trajectory::computeTrajectoryStraightLineToPoint(targetPosition, endPosition);
        robot.setTrajectoryToFollow(traj);
        wasMoveSuccessful = robot.waitForTrajectoryFinished();
        //~ robot.moveRail(0.3);
        //~ robot.servos_.moveSuction(true);
        bool wasBlueDropped = false;
        if (wasMoveSuccessful)
        {
            // Drop blue atom.
            wasBlueDropped = true;

            //~ robot.servos_.tapOpen();
            //~ robot.servos_.openTube(suctionOrder[0]);
            //~ usleep(300000);
            //~ robot.servos_.tapClose();
            //~ robot.servos_.closeTube(suctionOrder[0]);
            robot.updateScore(6);   // One correct drop.
            targetPosition = robot.getCurrentPosition();
            traj = miam::trajectory::computeTrajectoryStraightLine(targetPosition, -150);
            robot.setTrajectoryToFollow(traj);
            robot.waitForTrajectoryFinished();
        }

        // Go drop green atom.
        targetPosition = robot.getCurrentPosition();
        positions.clear();
        positions.push_back(targetPosition);
        targetPosition.x = 750;
        targetPosition.y = 1250;
        positions.push_back(targetPosition);
        targetPosition.x = 450 + CHASSIS_FRONT;
        positions.push_back(targetPosition);
        traj = miam::trajectory::computeTrajectoryRoundedCorner(positions, 150.0, 0.05);
        robot.setTrajectoryToFollow(traj);
        wasMoveSuccessful = robot.waitForTrajectoryFinished();

        bool wasGreenDropped = false;
        if (wasMoveSuccessful)
        {
            // Drop green atom.
            wasGreenDropped = true;

            //~ robot.servos_.tapOpen();
            //~ robot.servos_.openTube(suctionOrder[1]);
            //~ usleep(300000);
            //~ robot.servos_.tapClose();
            //~ robot.servos_.closeTube(suctionOrder[1]);
            robot.updateScore(6);   // One correct drop.
            targetPosition = robot.getCurrentPosition();
            traj = miam::trajectory::computeTrajectoryStraightLine(targetPosition, -150);
            robot.setTrajectoryToFollow(traj);
            robot.waitForTrajectoryFinished();
        }

        // Finally, go drop red atom.
        targetPosition = robot.getCurrentPosition();
        positions.clear();
        positions.push_back(targetPosition);
        targetPosition.x = 750;
        targetPosition.y = 1550;
        positions.push_back(targetPosition);
        targetPosition.x = 450 + CHASSIS_FRONT;
        positions.push_back(targetPosition);
        traj = miam::trajectory::computeTrajectoryRoundedCorner(positions, 150.0, 0.05);
        robot.setTrajectoryToFollow(traj);
        wasMoveSuccessful = robot.waitForTrajectoryFinished();

        if (wasMoveSuccessful)
        {
            // Drop everything.
            //~ robot.servos_.tapOpen();
            //~ robot.servos_.openTube(0);
            //~ robot.servos_.openTube(1);
            //~ robot.servos_.openTube(2);
            robot.updateScore(6);   // One correct drop.
            // Update score if needed.
            if (!wasBlueDropped)
                robot.updateScore(1);
            if (!wasGreenDropped)
                robot.updateScore(1);
        }
    }
}

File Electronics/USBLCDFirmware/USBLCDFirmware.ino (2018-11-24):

/***********************************
Matrix-orbitalish compatible LCD driver with USB and Serial
For use with Teensy 1.0 core on AT90USB162 chips

This file is a modification of Adafruit firmware from
https://github.com/adafruit/Adafruit-USB-Serial-RGB-Character-Backpack

that integrates the changes done by the addon board: the 4 GPIOs and RX/TX lines were
reconverted into three buttons and 3 LEDs.
Consequently:

 - the serial (UART) interface is disabled.
 - the commands MATRIX_GPO_OFF, MATRIX_GPO_ON, MATRIX_GPO_START_ONOFF, MATRIX_BAUDRATE now have not effect.
 - added command ADDON_GET_BUTTON_STATE 0xAA: return a single char containing 0b10000d2d1d0 where d1 is the state of
buttong i.
 - added command ADDON_SET_LED_STATE 0xAB: expert one parameter of the form 0b00000d2d1d0 where di is the state of
led i (1 for on, zero for off).

To compile, use arduino-1.0.5 with teensyduino 1.16. Get .hex from /tmp/ directory. Wire the board using ArduinoISP wiring and code.
Flash with:
avrdude -p usb162 -P /dev/ttyACM0 -c avrisp -b 19200 -U flash:w:USBLCDFirmware.cpp.hex -v

---> http://www.adafruit.com/category/63_96

Adafruit invests time and resources providing this open source code,
please support Adafruit and open-source hardware by purchasing
products from Adafruit!

Written by Limor Fried/Ladyada  for Adafruit Industries.
BSD license, check license.txt for more information
All text above must be included in any redistribution
****************************************/


#include <LiquidCrystal.h>
#include <EEPROM.h>
#include <util/delay.h>

// uncomment below to have the display buffer echo'd to USB serial (handy!)
//#define USBLCDDEBUG 1

// this will echo a 'buffer' showing what the display thinks is showing
//#define USBECHOBUFFER 1

// this will echo incoming chars
//#define USBECHOCHARS 1

#define D4  1  // PD1
#define D5  4  // PD4
#define D6  5  // PD5
#define D7  6  // PD6
#define RS  12 // PB4
#define RW  13 // PB5
#define EN  14 // PB6

LiquidCrystal lcd(RS, RW, EN, D4, D5, D6, D7);

// Disable uart to use as GPIO
// This line defines a "Uart" object to access the serial port
// HardwareSerial Uart = HardwareSerial();

// connect these to the analog output (PWM) pins!
#define REDLITE 0              // D0
#define GREENLITE 18           // C5
#define BLUELITE 17            // C6
#define CONTRASTPIN 15         // B7

#define GPO_1  8 // PB0
#define GPO_2  20 // PC2
#define GPO_3  19 //PC4
#define GPO_4  16 //PC7
uint8_t GPO[] = {GPO_1, GPO_2, GPO_3, GPO_4};

// see a list of matrix orbital commands here (we dont support -all-)
//http://www.matrixorbital.ca/manuals/LCDVFD_Series/LCD2041/LCD2041.pdf

/******** Communication commands */
//#define MATRIX_I2CADDR 0x33      // not supported
#define MATRIX_BAUDRATE 0x39       // 1 arg
//#define MATRIX_BAUDRATE2 0xA4      // not supported

/******** text commands */
#define MATRIX_AUTOSCROLL_ON 0x51
#define MATRIX_AUTOSCROLL_OFF 0x52
#define MATRIX_CLEAR 0x58
#define MATRIX_CHANGESPLASH 0x40  // COL * ROW chars!
#define MATRIX_AUTOWRAPLINE_ON 0x43
#define MATRIX_AUTOWRAPLINE_OFF 0x44
#define MATRIX_SETCURSOR_POSITION 0x47    // 2 args: col, row
#define MATRIX_HOME 0x48
#define MATRIX_MOVECURSOR_BACK 0x4C
#define MATRIX_MOVECURSOR_FORWARD 0x4D
#define MATRIX_UNDERLINECURSOR_ON 0x4A
#define MATRIX_UNDERLINECURSOR_OFF 0x4B
#define MATRIX_BLOCKCURSOR_ON 0x53
#define MATRIX_BLOCKCURSOR_OFF 0x54

/****** special chars */
#define MATRIX_CUSTOM_CHARACTER 0x4E  // 9 args: char #, 8 bytes data
#define MATRIX_SAVECUSTOMCHARBANK 0xC1  // 9 args: char #, 8 bytes data
#define MATRIX_LOADCUSTOMCHARBANK 0xC0  // 9 args: char #, 8 bytes data
/***** Numbers & Bargraphs */
// not supported until we know what these look like
//#define MATRIX_PLACEMEDIUMDIGIT 0x6F
/***** display func */
#define MATRIX_DISPLAY_ON  0x42    // backlight. 1 argument afterwards, in minutes
#define MATRIX_DISPLAY_OFF  0x46
#define MATRIX_SET_BRIGHTNESS 0x99 // 1 arg: scale
#define MATRIX_SETSAVE_BRIGHTNESS 0x98 // 1 arg: scale
#define MATRIX_SET_CONTRAST 0x50 // 1 arg
#define MATRIX_SETSAVE_CONTRAST 0x91 // 1 arg
/***** GPO commands */
#define MATRIX_GPO_OFF 0x56
#define MATRIX_GPO_ON 0x57
#define MATRIX_GPO_START_ONOFF 0xC3

/***** Extra Adafruit commands */
#define EXTENDED_RGBBACKLIGHT 0xD0  // 3 args - R G B
#define EXTENDED_SETSIZE 0xD1  // 2 args - Cols & Rows
#define EXTENDED_TESTBAUD 0xD2  // zero args, prints baud rate to uart

/***** Extra commands for addon shield */
#define ADDON_GET_BUTTON_STATE 0xAA
#define ADDON_SET_LED_STATE 0xAB
 
 // Button pins, from left to right
uint8_t BUTTONS[] = {16, 19, 20}; 
 // LED pins, from left to right
uint8_t LEDS[] = {8, 3, 2}; 
 

#define MATRIX_STARTL_COMMAND 0xFE
//#define MATRIX_END_COMMAND 0x9A

// storage of the current backlight state
#define COLS_ADDR 0
#define ROWS_ADDR 1
#define SPLASH_ADDR 2
#define BACKLIGHT_R_ADDR 100
#define BACKLIGHT_G_ADDR 101
#define BACKLIGHT_B_ADDR 102
#define BACKLIGHT_STATE_ADDR 103
#define BACKLIGHT_BRIGHTNESS_ADDR 104
#define AUTOSCROLL_ADDR 105
#define BAUDRATE_ADDR 106  // and 107, 108
#define CONTRAST_ADDR 109
#define CUSTOMCHARBANKS_ADDR 110
// 110 thru 430 !
#define GPO_1_START_ONOFF_ADDR 431
#define GPO_2_START_ONOFF_ADDR 432
#define GPO_3_START_ONOFF_ADDR 434
#define GPO_4_START_ONOFF_ADDR 435
#define LAST_ADDR 436
#define EEPROM_END 511

uint8_t COLS = EEPROM.read(COLS_ADDR);
uint8_t ROWS = EEPROM.read(ROWS_ADDR);
uint8_t x, y;

extern unsigned int __bss_end;
extern unsigned int __heap_start;
extern void *__brkval;
int freeMemory() {
  int free_memory;

  if ((int)__brkval == 0)
     free_memory = ((int)&free_memory) - ((int)&__bss_end);
  else
    free_memory = ((int)&free_memory) - ((int)__brkval);

  return free_memory;
}

void setup() {
  if (getBaud() > 115200) {
    setBaud(9600);
  } else {
    setBaud(getBaud());
  }
  if (COLS > 20) COLS = 20;
  if (ROWS > 4) ROWS = 4;

  pinMode(CONTRASTPIN, OUTPUT);
  pinMode(REDLITE, OUTPUT);
  pinMode(GREENLITE, OUTPUT);
  pinMode(BLUELITE, OUTPUT);
  
  // Set buttons as input, pullup, and leds as output.
  for(uint8_t i = 0; i < 3; i++)
  {
    pinMode(BUTTONS[i], INPUT);
    digitalWrite(BUTTONS[i], HIGH);
    pinMode(LEDS[i], OUTPUT);
    digitalWrite(LEDS[i], LOW);
  }
  
  // for the initial 'blink' we want to use default settings:
  lcd.begin(16, 2);
  analogWrite(CONTRASTPIN, 50);  // test contrast
  analogWrite(REDLITE, 255);
  analogWrite(GREENLITE, 255);
  analogWrite(BLUELITE, 255);


  _delay_ms(250);

  // now setup the way we expect
  lcd.begin(COLS, ROWS);
  setContrast(getContrast());
  displayOn();
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

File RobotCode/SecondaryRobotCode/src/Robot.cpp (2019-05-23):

#include "Robot.h"
#include <thread>
#include <unistd.h>

const int START_SWITCH = CAPE_DIGITAL[0];

const double INITIAL_GYRO_BIAS = 0.0305;

// Update loop frequency
const double LOOP_PERIOD = 0.010;

Robot::Robot():
    AbstractRobot(),
    isIMUInit_(false),
    isScreenInit_(false),
    IRFrontLeft_(0),
    IRFrontRight_(0),
    IRBackLeft_(0),
    IRBackRight_(0),
    isFrontDetectionActive_(false),
    isBackDetectionActive_(false),
    hasDetectionStoppedRobot_(false),
    detectionStopTime_(0.0),
    startupStatus_(startupstatus::INIT),
    initMotorState_(0),
    nConsecutiveIRState_(0),
    gyroValue_(0.0),
    frontDetectionThreshold_(500),
    backDetectionThreshold_(500)
{
    kinematics_ = DrivetrainKinematics(robotdimensions::wheelRadius,
                                       robotdimensions::wheelSpacing,
                                       robotdimensions::encoderWheelRadius,
                                       robotdimensions::encoderWheelSpacing);
    // Update trajectory config.
    miam::trajectory::setTrajectoryGenerationConfig(robotdimensions::maxWheelSpeedTrajectory,
                                                    robotdimensions::maxWheelAccelerationTrajectory,
                                                    robotdimensions::wheelSpacing);

    // Create logger.
    std::time_t t = std::time(nullptr);
    char timestamp[100];
    std::strftime(timestamp, sizeof(timestamp), "%Y%m%dT%H%M%SZ", std::localtime(&t));
    std::string filename = "/tmp/log" + std::string(timestamp) + ".csv";
    std::string headers = getHeaderStringList();
    // Log robot dimensions in header.
    std::string info = "wheelRadius:" + std::to_string(robotdimensions::wheelRadius) + \
                        "_wheelSpacing:" + std::to_string(robotdimensions::wheelSpacing) + \
                        "_stepSize:" + std::to_string(robotdimensions::stepSize);

    logger_ = Logger(filename, "Secondary robot", info, getHeaderStringList());

    // Set initial positon.
    RobotPosition initialPosition;
    initialPosition.x = 0;
    initialPosition.y = 0;
    initialPosition.theta = 0;
    currentPosition_.set(initialPosition);
    currentBaseSpeed_.linear = 0;
    currentBaseSpeed_.angular = 0;

    // Set PIDs.
    PIDLinear_ = miam::PID(controller::linearKp, controller::linearKd, controller::linearKi, 0.2);
    PIDAngular_ = miam::PID(controller::rotationKp, controller::rotationKd, controller::rotationKi, 0.15);
}

bool Robot::initSystem()
{
    bool allInitSuccessful = true;

    // Move the servos up ; no init required.
    robot.moveServos(false);

    if (!isScreenInit_)
    {
        isScreenInit_ = robot.screen_.init(&I2C_1);
        if (!isScreenInit_)
        {
            #ifdef DEBUG
                std::cout << "[Robot] Failed to init communication with screen." << std::endl;
            #endif
            allInitSuccessful = false;
        }
        else
        {
            robot.screen_.setTextCentered("Initializing", 0);
            robot.screen_.setBacklight(true, true, true);
        }
    }
    if (!isIMUInit_)
    {
        isIMUInit_ = imu_initDefault(&imu_, &I2C_1, false);
        if (!isIMUInit_)
        {
            #ifdef DEBUG
                std::cout << "[Robot] Failed to init communication with IMU." << std::endl;
            #endif
            allInitSuccessful = false;
            robot.screen_.setTextCentered("IMU init failed", 0);
            robot.screen_.setBacklight(true, false, false);
        }
    }
    if (!isStepperInit_)
    {
        // Motor config values - 42BYGHW810, 2.0A.
        const int MOTOR_KVAL_HOLD = 0x25;
        const int MOTOR_BEMF[4] = {0x36, 0x172E, 0xC, 0x33};

        // Compute max stepper motor speed.
        int maxSpeed = robotdimensions::maxWheelSpeed / robotdimensions::wheelRadius / robotdimensions::stepSize;
        int maxAcceleration = robotdimensions::maxWheelAcceleration / robotdimensions::wheelRadius / robotdimensions::stepSize;
        // Initialize both motors.
        stepperMotors_ = miam::L6470("/dev/spidev1.0", 2);
        isStepperInit_ = stepperMotors_.init(maxSpeed, maxAcceleration, MOTOR_KVAL_HOLD,
                                             MOTOR_BEMF[0], MOTOR_BEMF[1], MOTOR_BEMF[2], MOTOR_BEMF[3]);
        if (!isStepperInit_)
        {
            #ifdef DEBUG
                std::cout << "[Robot] Failed to init communication with stepper motors." << std::endl;
            #endif
            allInitSuccessful = false;
            robot.screen_.setTextCentered("Motor init failed", 0);
            robot.screen_.setBacklight(true, false, false);
        }
        else
            stepperMotors_.highZ();
    }
    if(allInitSuccessful)
        gpio_digitalWrite(CAPE_LED[1], 0);
    else
        gpio_digitalWrite(CAPE_LED[1], 1);
    return allInitSuccessful;
}
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

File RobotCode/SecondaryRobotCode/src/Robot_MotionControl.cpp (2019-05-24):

#include "Robot.h"

// Control of the robot motion on the table.
// Trajectory list handling, trajectory following, obstacle avoidance.

// Obstacle avoidance parameters
double const IR_START_TIMEOUT = 5.0; // Disable IR detection for the first n seconds of the match, to be sure to leave the starting zone safely.

double const FRONT_DETECTION_DISTANCE = 750;    // Distance between center of the robot and detected obstacle.
double const BACK_DETECTION_DISTANCE = 750;

int const N_VIEWS_FOR_STOP = 2; // Number of consecutive views to stop the robot.
int const N_MISS_FOR_START = 5; // Number of consecutive non-detection to restart robot.

bool Robot::handleDetection()
{
    // Read IR sensors.
    IRFrontLeft_ = gpio_analogRead(CAPE_ANALOG[1]);
    IRFrontRight_ = gpio_analogRead(CAPE_ANALOG[4]);
    IRBackLeft_ = gpio_analogRead(CAPE_ANALOG[2]);
    IRBackRight_ = gpio_analogRead(CAPE_ANALOG[3]);

    // Determine if a robot is visible in front or behind the robot.
    isFrontDetectionActive_ = (IRFrontLeft_ > robot.frontDetectionThreshold_ || IRFrontRight_ > robot.frontDetectionThreshold_);
    isBackDetectionActive_ = (IRBackLeft_ > robot.backDetectionThreshold_ || IRBackRight_ > robot.backDetectionThreshold_);

    // Set LED status
    gpio_digitalWrite(CAPE_LED[1], isFrontDetectionActive_ || isBackDetectionActive_);

    bool shouldRobotStop = false;

    bool isGoingForward = true;
    // Determine if there is an obstacle in the direction we are going,
    if (trajectoryPoint_.linearVelocity > 0.01 && isFrontDetectionActive_)
        isGoingForward = true;
    else if (trajectoryPoint_.linearVelocity < -0.01 && isBackDetectionActive_)
        isGoingForward = false;
    else
        return false; // If we have no forward or backward desired velocity (i.e. point turn), no need to do any detection.

    // Find obstacle position.
    RobotPosition obstaclePosition;
    if (isGoingForward)
        obstaclePosition.x = FRONT_DETECTION_DISTANCE;
    else
        obstaclePosition.x -= BACK_DETECTION_DISTANCE;

    RobotPosition robotPosition = getCurrentPosition();
    obstaclePosition = obstaclePosition.rotate(robotPosition.theta) + robotPosition;

    // If the obstacle is outside of the playing field, ignore it.
    if (obstaclePosition.x > 0 && obstaclePosition.x < 3000 && obstaclePosition.y > 0 && obstaclePosition.y < 2000)
        shouldRobotStop = true;

    if (!hasMatchStarted_)
        return false;
    if (currentTime_ - matchStartTime_ < IR_START_TIMEOUT)
        return false;
    //~ return shouldRobotStop;
    return false;
}


bool Robot::followTrajectory(Trajectory *traj, double const& timeInTrajectory, double const & dt)
{
    // Get current trajectory state.
    trajectoryPoint_ = traj->getCurrentPoint(timeInTrajectory);

    // Compute targets for rotation and translation motors.
    BaseSpeed targetSpeed;

    // Feedforward.
    targetSpeed.linear = trajectoryPoint_.linearVelocity;
    targetSpeed.angular = trajectoryPoint_.angularVelocity;

    // Compute error.
    RobotPosition currentPosition = currentPosition_.get();
    RobotPosition error = currentPosition - trajectoryPoint_.position;

    // Rotate by -theta to express the error in the tangent frame.
    RobotPosition rotatedError = error.rotate(-trajectoryPoint_.position.theta);

    trackingLongitudinalError_ = rotatedError.x;
    trackingTransverseError_ = rotatedError.y;

    // Change sign if going backward.
    if(trajectoryPoint_.linearVelocity < 0)
        trackingTransverseError_ = - trackingTransverseError_;
    trackingAngleError_ = miam::trajectory::moduloTwoPi(currentPosition.theta - trajectoryPoint_.position.theta);

    // If we are beyon trajector end, look to see if we are close enough to the target point to stop.
    if(traj->getDuration() <= timeInTrajectory)
    {
        if(trackingLongitudinalError_ < 3 && trackingAngleError_ < 0.02 && motorSpeed_[RIGHT] < 100 && motorSpeed_[LEFT] < 100)
        {
            // Just stop the robot.
            motorSpeed_[0] = 0.0;
            motorSpeed_[1] = 0.0;
            return true;
        }
    }

    // Compute correction terms.

    // If trajectory has an angular velocity but no linear velocity, it's a point turn:
    // disable corresponding position servoing.
    if(std::abs(trajectoryPoint_.linearVelocity) > 0.1 || std::abs(trajectoryPoint_.angularVelocity) < 1e-4)
        targetSpeed.linear += PIDLinear_.computeValue(trackingLongitudinalError_, dt);

    // Modify angular PID target based on transverse error, if we are going fast enough.
    double angularPIDError = trackingAngleError_;
    if(std::abs(trajectoryPoint_.linearVelocity) > 0.1 * robotdimensions::maxWheelSpeed)
        angularPIDError += controller::transverseKp * trajectoryPoint_.linearVelocity / robotdimensions::maxWheelSpeed * trackingTransverseError_;
    targetSpeed.angular += PIDAngular_.computeValue(angularPIDError, dt);

    // Invert velocity if playing on right side.
    if (isPlayingRightSide_)
        targetSpeed.angular = -targetSpeed.angular;

    // Convert from base velocity to motor wheel velocity.
    WheelSpeed wheelSpeed = kinematics_.inverseKinematics(targetSpeed);
    // Convert to motor unit.
    motorSpeed_[RIGHT] = wheelSpeed.right / robotdimensions::stepSize;
    motorSpeed_[LEFT] = wheelSpeed.left / robotdimensions::stepSize;

    return false;
}
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

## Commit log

2017-11-21 [ProgrammationBBB] Ajout du dossier ProgrammationBBB
    - Ajout de la bibliothèque BBBEurobot
    - Ajout du programme de test TestADNS (pour démo de l'usage de BBBEurobot et pour un exemple de fichier CMakeLists)
    - Ajout d'un tuto pour la configuration d'un environnement de cross-compilation.
    - Mise à jour du README principal + README dans ProgrammationBBB.
2017-11-27 [Programmation] Ajout du filtre de kalman et mise a jour des CMakeLists
    - Ajout des liens vers libpthread et libmath lors de la compilation.
    - Ajout de l'option make install a TestADNS
    - Cleanup.
    - Ajout du code du filtre de Kalman a BBBEurobot.
2017-12-09 [ProgrammationBBB] Ajout de la documentation et de l'initialisation.
    - Ajout du dossier doc générant une documentation doxygen de BBBEurobot.
    - Ajout de l'overlay Eurobot-00A0.dts pour activer les ports série.
    - Ajout de BBBGpio - gestion des ports série uniquement.
    - Supression de IRReciever (inutile pour le moment).
    - Mise a jour de TestADNS.
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2018-01-27 [BBBEurobot] Rework of I2C-Wrapper.
    Reimplement I2C wrappers to give better debug info, and to be thread-safe even when using several I2C ports.
    This is done by creating a new I2CAdapter structure to link port name and mutex.
    [I2C-Wrapper.c]
2018-01-28 [BBB-Eurobot] Add driver for color sensor. Change types of some I2C functions.
    Most parameters of the I2C drivers should be of type guint8 (i.e. unsigned char i.e. uint8_t) instead of int.
    This was changed in I2C-Wrapper and in some other drivers.
2018-01-29 [BBBEurobot] Add driver for LCD screen. Update documentation.
    Note that the LCD driver is not fully fonctional yet: the screen
    only works with one line activated.
2018-02-08 [BBB-Eurobot] Fix driver for TCS3472 Color Sensor after code testing. Fix bug in BBB_enableCape where early return canceled digital pin configuration.
2018-02-23 [BBB-Eurobot] Update IMU driver to work with Pololu MiniIMU-V5 instead of V3.
    Update DTO file - set I2C frequency to 400kHz instead of 100kHz.
    Fix bug in enabling GPIOs.
2018-02-25 [BBBEurobot] Testing of servo driver and analog input code.
    Minor code fixup.
    [I2C-Wrapper.c]
2018-02-27 [BBB-Eurobot] Fix LCD driver after component test.
2018-03-01 [BBB-Eurobot] Update SPI handling.
    - Modify SPI-related struct. to have default frequency at 800kHz instead
    of taking 'speed' as an argument.
    - Modify ADNS9800 api to be more consistent with the rest of the library.
2018-03-03 [BBB-Eurobot] Release of V1.0
    - The library has been fully tested at least once, except for L6470 driver (but it is similar
    to the one used last year).
    - Added SPI wrapper class, to begin merging the two SPI implementations (WIP).
    - Cape I2C are now I2C adpater directly instead of strings.
2018-03-03 [programming] Added test script for all sensors.
    Add TestSensors code, that test all components of the robot except motors.
    This code tests:
    - digital input and output (leds)
    - analog input
    - IMU
    - Mouse sensor
    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
2018-03-03 [programming] Remove obsolete TestADNS project.
    This project is replaced by the more complete TestSensors project.
    [Main.c]
2018-03-17 [BBB-Eurobot] Full reimplementation of L6470 driver.
    After reading the datasheet, implement SPI communication in a way that is
    more consistent whith what is being asked by the driver.
    The previous code was doing independant SPI operation for each byte transfer,
    while the current code treats one device command as a single transfer.
    The new implementation also ensures zeros are sent when no command is needed,
    removing the frequen "command no exec" error.
2018-03-17 [overlay] Add UART4 to device tree overlay file (for new servo driver).
2018-03-18 [BBBEurobot] Make L6470_getError verbose.
    L6470_getError now prints human-readable errors.
2018-03-23 [BBB-Eurobot] Add driver for Pololu Maestro servo driver board.
    Note that this code only supports writing to the servo board,
    reading functions are not implemented.
2018-04-08 [BBB-Eurobot] Fixup of servo driver.
    Maestro servo driver tested and functional.
2018-04-08 [BBB-Eurobot] Fix minor error in L6470 driver.
    Wrong Command and Bad Command errors returned by the IC are active
    high, unlike the other wich are active low. This wasn't taken
    into account, leading to erronous error messages being printed.
2018-04-20 [eurobotCode] Fix code according to March 4th Skype
    - Fix currentTime & lastTime in MotionController.c
    - Replace timerThread with a g_timeout to end the match
    [MainLoop.c]
2018-04-20 [Eurobot Code] Many minor code changes.
    - Robot: replace RobotTarget.parameter by RobotTarget.RobotPosition
    - MotionController: change motor current from 1.5A running (1.8 blocked) to 2.0A - 2.1A.
    - Main: add mouse sensor init.
    - Strategy: uncomment testing trajectory.
    [MainLoop.c]
2018-04-20 Full rewrite of robot positionning and motion on table.
    The code now has an architecture closer to that of last year, with localisation and
    constrol separated:
    - file Localisation.c implements a thread that runs robot position estimation and logging.
    - file MotionController implements blocking functions for robot motion (rotation, translation,
    goTo).
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2018-04-20 [EurobotCode] Add trajectory for rotation.
    Previously, rotations were done using a step input. This is replaced
    by a velocity trapezoid, generating a continuous motion.
2018-04-20 [EurobotCode] Fixup of motion, wait and infrared.
    Test waitForStart and infrared sensors, fixed code bugs.
    Test trapezoid trajectory for rotation, update PID gains.
    Fix error in computeRotationAngle.
    [MainLoop.c]
2018-04-20 [Eurobot] Update strategy and servo motion after further testing. Tune motion controller for better performances.
2018-05-03 [BBB-Eurobot] Bugfix and tunning.
    - Make LCD driver thread safe by adding a mutex when writing a character to the screen.
    - Update Kalman filter gains.
    - Update ADNS9800 sensor.
2018-05-05 [BBB-Eurobot] Raise default L6470 stall and OCD thersholds.
2018-05-06 [EurobotCode] Change the way motors are stopped.
    Previously motion_stopMotors setted them to high-impedence instantaneously,
    thus no braking was applied. This has been fixed.
    Change velocity profile to have stronger deceleration than acceleration.
    [MainLoop.c]
2018-05-06 [EurobotCode] Remove logging of unused gyroX and gyroY, add logging of Kalman bias.
2018-05-06 [EurobotCode] Change avoidance so that the robot will not wait for longer than needed. Increase IR reading frequency.
    If two successive readings give a no-robot call, motion can start again.
    [MainLoop.c]
2018-05-09 [BBB-Eurobot] Ignore stall errors.
2018-05-13 [Eurobot] Code of match 4 - modify IR code.
    IR sensors are now filtered using a moving average filter, instead of waiting
    for consecutive similar values. Add IR log.
2018-06-27 Update all READMEs, translate them all to English.
    Change folder name to English, translate wiring diagram, translate all
    README files.
2018-07-08 [BBBEurobot] Bugfix in IMU driver.
    - Update documentation.
    - Fix magnetometer scaling.
    - Update config register for more sensible ODR selection.
2018-07-08 [BBBEurobot] Add debug/release build option.
    Code can now be built in debug or release. In release mode, -O3 flag
    is used and errors that print data to the console ouptut are silent.
    [I2C-Wrapper.c]
2018-07-08 [EurobotCode] Refactor IR handling.
    - IR sensors are now checked in the localisation thread: this makes
    logging much easier.
    - Rename localisationThread to SensorUpdate thread, since this is what
    it's doing.
2018-08-14 Full code rework to work with Raspberry Pi.
    - Rename Code_BBB to RobotCode.
    - Rework BBBEurobot library to be more generic in order to work with the Raspberry Pi as well.
    New library, MiAMEurobot, works for both processors. Different includes are used to declare the serial ports
    of each board, but the rest is common.
    - Add code for an arduino to read a serial encoder and send it through UART.
    - Add test code for new drive train: this code servos a stepper motor onto an encoder through an arduino.
    - Add folder containing config steps for a Raspberry Pi.
    [I2C-Wrapper.c, Main.c, MainLoop.c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]
2018-08-15 [Drivetrain] Add second encoder.
    - Add handling of second encoder for Arduino, using PCINT instead of ext interrupts.
    - Add handling of second encoder in C code.
    - Lower encoder resolution do 1024 (4096 ticks/rev) as current Arduino code is not
    fast enough to work at max resolution.
    - Remove deadcode in python miam_plot.
    - Update config README.
2018-08-15 [ArduinoSlave] Speed up interrupt code.
    - This version of the code has been tested with both encoders at 1024 resolution, going at 7revolution/s
    (1m/s with current wheel diameter).
    - Added info in uCListner.h about how to create a constant symbolic link pointing to the connected Arduino
    (to prevent USB name change when replugging).
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2018-08-26 [Electronics] Add general diagram and Raspberry shield first draft.
    - Add a planned general wiring diagram for the main robot.
    - Create Kicad library and project for a Raspberry Pi interface shield. Start of design.
    [RPiShield.kicad_pcb, RPiShield.sch]
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2018-09-17 [Electronics] Added temporary version of PowerDistribution PCB.
    [PowerDistribution.kicad_pcb, PowerDistribution.sch]
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2018-10-13 [Drivetrain test] Full rework of drivetrain code to work with new trajectories.
    - Start shifting code to C++.
    - Implement trajectory following - for now, only feedforward term is used. Trajectory
    following is done inside the low-level thread, which runs at a fixed frequency. A
    strategy thread feeds it once in a while a trajectory to follow. Logging is done by the low-level
    component. This code was tested and seems to be working.
    [MainLoop.c, Robot.cpp, uCListener.c]
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2018-11-01 [RobotCode/DrivetrainTest] Improve Arduino communication.
    Add checksum to prevent wrong data reading.
    Lower Arduino output datarate, the current code doesn't need to work faster
    than 100Hz. In fact the Raspberry Pi seems to exibit up to 4ms of latency
    when using USB->uart - this is not a problem for now...
    [uCListener.c]
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2018-11-24 [Electronics] Add LCDButtons project.
    - Add LCDButtons, a small PCB addon to adafruit USB LCD shield.
    - Add firmware code for shield uController to support new PCB.
    - Update wiring diagram.
    [LCLDButtons.kicad_pcb, LCLDButtons.sch]
2018-12-03 [Electronics] PCB - first complete version.
    [LCLDButtons.kicad_pcb, LCLDButtons.sch, PowerDistribution.kicad_pcb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]
2018-12-03 [MiAMEurobot] Minor improvements
    - Minor fix to PID and UART class.
    - Add trajectories to library main header.
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2019-02-16 [MiAMEurobot][DrivetrainTest] Update library and add composent tests.
    - MiAMEurobot: many minor improvements and C++ code update. Added missing files.
    - Create unit tests for testing individual components, mostly made for the wiring.
    [L6470Test.cpp, LCDDriver.cpp, MaestroServoDriver.cpp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]
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2019-02-21 [MiAMEurobot] Add function for computing kinematics ; change convention to direct frame
    - Add DrivetrainKinematics for computing the kinematics of the drivetrain in a unified manner.
    - Switch back to using a standard direct frame (y upward and no longer downward). This is still work
    in progress, some old convention may still be present.
    [DrivetrainKinematics.cpp]
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2019-02-22 [MiAMEurobot/trajectory] Fix DrivetrainKinematics
    * inverseKinematics lacked some braces
    [DrivetrainKinematics.cpp]
2019-02-22 [MiAMEurobot/trajectory] Fix (bis) DrivetrainKinetics
    * add some 2.0's
    [DrivetrainKinematics.cpp]
2019-02-23 [MiAMEurobt / MainRobotCode] Fixup after real robot testing
    - [MiAMEurobot] Fix bug in kinematics
    - [MainRobotCode] Add partial servo configuration after testing.
    - [MainRobotCode] Robot dimension parameter tunning.
    [DrivetrainKinematics.cpp, Robot.cpp, ServoHandler.cpp]
2019-02-24 [miam_py] Bugfixes and enhancements.
    - Fix miam_plot crash when asking to draw odd numbers of plots.
    - Add grid to miam_plot axes.
    - Improve layout of miam_plot to enhance readability.
    - Handle aspect ratio in miam_analyse_tracking.
    - Switch whole project from tabs to spaces.
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2019-03-10 [MainRobotCode][ArduinoSlave] Add identification message for Arduino.
    Arduino slave now sends an identification message on boot - this is checked for in uCListener to prevent
    mistaking another board for the Arduino slave.
    [MainLoop.cpp]
2019-03-17 [MiAMEurobot] Internal bug fixup<
    - Fix bug in L6470 driver where any value read from the boards corresponded to the first controller only.
    - Raspberry pi GIOP: fix bug in gpio output causing all outputs to toggle together.
    [L6470Driver.cpp, PiGPIO.cpp]
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2019-03-25 [MiAMEurobot] Fix L6470 not being reset due to wrong command.
    [L6470Driver.cpp]
2019-03-25 [MainRobotCode] Add code for reading potentiometer position.
    - Update arduino code to read potentiometer off analog 0.
    - Raspberry code: read and log potentiometer position.
    - Update CMakeLists.txt for correct debug support.
    [Robot.cpp]
2019-03-26 [MiAMEurobot] Update L6470 driver to support external crystal clock.
    This improves tracking accuracy significatively, as the internal oscillator
    is wrong by about 5%.
    [L6470Driver.cpp]
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2019-03-28 [RobotCode] Update beaglebone support ; beginning of code for Secondary robot.
    - Change the way overlays are loaded because the previous overlay no longer
    works after kernel update ; for now, use separate off-the-shelf overlays.
    - Add init code with communication to both stepper motors and IMU ; tested.
    [MainLoop.cpp, Robot.cpp]
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2019-04-12 [RobotCode] Fixup and enhance debugging for robot servoing.
    - MiAMEurobot: add function to rotate a position and to get the PID correction term.
    - MainRobotCode: add debug variables to the log for PID analysis and tunning. Correct
    some bugs in trajectory tracking formulation. Fix trajectory generation velocity.
    - miam_analyse_tracking: use the newly available fields for enhance debugging.
    [MainLoop.cpp, Robot.cpp]
2019-04-12 [MiAMEurobot] Fix errors when computing circle trajectories.
    This is a remanant of the sign change on the Y axis that wasn't replicated everywhere.
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2019-04-22 [MiAMEurobot] Add AbstractRobot class.
    - Add abstract class representing a robot, for doing basic operations
    and sharing a common architecture between both projects.
    - Rework both robot code to comply with AbstractRobot class.
    [AbstractRobot.cpp, MainLoop.cpp, Robot.cpp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]
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2019-04-24 [SecondaryRobot] Test secondary robot code ; tuning and some fixup.
    - Test robot control and basic IR detection.
    - Tune wheel size and spacing.
    - Bugfix: use recursive_mutex in L6470 driver to prevent deadlock at code exit.
    [MainLoop.cpp, Robot.cpp, Robot_MotionControl.cpp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]
2019-04-26 [SecondaryRobot] Complete init and side choice.
    - Complete init function with user interface. Missing: reading starting
    jack value as this component is not yet mounted on the robot.
    - Modify localisation and tracking code to work on both sides.
    - MainRobotCode: add missing thread detach.
    [Robot.cpp, Robot_MotionControl.cpp]
2019-04-27 Fix bug in LCD driver. Various improvements to secondary robot code.
    [LCDDriver.cpp, MainLoop.cpp, Robot.cpp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]
2019-04-27 [MiAMEurobot] BBBGpio: add try/catch to prevent segfault.
    Secondary robot code: fix purple side miror. Use PID for correcting open-loop
    velocity trajectory based on motor position.
    [MainLoop.cpp, Robot.cpp, Robot_MotionControl.cpp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]
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2019-04-29 [MainRobotCode] Add missing strategy file.
    [Strategy.cpp]
2019-05-01 [MiAMEurobot] Rework and improve Lidar code.
    - Clean up code to remove bugs due to bad code writing.
    - Perform detected robot removal based on time data - this enables keeping an
    obstacle for more than a revolution, yielding a more stable detection.
    [RPLidarHandler.cpp]
2019-05-11 Secondary robot code update.
    Add gyro feedback for correcting robot angle.
    Add IR calibration procedure.
    [Robot.cpp, Robot_MotionControl.cpp, Strategy.cpp]
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2019-05-11 [RobotCode] Bugfix to both robot codes. Working code for secondary robot ; main robot: Lidar and obstacle avoidance are still TODOs.
    [AbstractRobot.cpp, Robot.cpp, Robot_MotionControl.cpp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]
2019-05-11 [MiamEurobot] Update LCDScreen to work asyncronously.
    - LCDScreen now works in a background thread, preventing client code jamming.
    - Secondary robot: display continuously IR data.
    [LCDDriver.cpp, Robot.cpp]
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2019-05-24 Funny action: update code after tunning.
    Main robot: code update.
    - fix rail motion.
    - add arm servos.
    - update strategy to work with arm servos.
    [ArduinoFunnyAction.ino, Robot.cpp, Robot_MotionControl.cpp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]
2019-05-25 Main Robot: update code: working strategy with no avoidance.
    [ArduinoFunnyAction.ino, Robot.cpp, ServoHandler.cpp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]
2019-05-25 added beginning of lidar based avoidance
    [Robot.cpp, Robot_MotionControl.cpp]
2019-05-25 Avoidance debug: basic working version with robot stopping when objects are in front.
    [AbstractRobot.cpp, Robot.cpp, Robot_MotionControl.cpp]
2019-05-25 [Detection] Working detection code - no avoidance present yet.
    [RPLidarHandler.cpp, Robot.cpp, Robot_MotionControl.cpp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]
2019-05-26 Git cleanup.
    - Add missing options to .gitignore file
    - Update READMEs.
    - Add missing PCB library link files.
2019-05-26 [MainRobot] Update strategy (not tested on table yet).
    - MiAMEurobot: fix typo in trajectory/Utilities.h
    - MainRobot: update code to include handling of last atoms.
    - Strategy viewer: update code to reflect new strategy and to be closer to the robot code.
    [MainRobotStrategy.cpp, Strategy.cpp]
2019-05-29 LidarHandler: fix memory bug. MainRobot: update strategy.
    [RPLidarHandler.cpp, Robot.cpp, Strategy.cpp]
2019-05-30 [MainRobot] Update avoidance to prevent deadlock.
    Robot now performs rotation and goes to next trajectory if needed.
    [Robot_MotionControl.cpp, Strategy.cpp]
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2019-05-31 Update strategy to prevent being stuck on the top of the field. Code of match 5.
    [Robot.cpp, ServoHandler.cpp, Strategy.cpp]
2019-06-01 Update servo position after servo replacement.
    [ServoHandler.cpp]
